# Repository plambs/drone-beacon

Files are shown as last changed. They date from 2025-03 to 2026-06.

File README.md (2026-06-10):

# Drone beacon

## Description

This repository contain the source code and schematic of the drone beacon that is mandatory for all flying models over 800gr in France.
The beacon use a ESP32 to send the model id over wifi and a gps module to know it position.

All model must be registered on [AlphaTango](https://alphatango.aviation-civile.gouv.fr/login.jsp)

This work is based on the work done by Arnaud Mazin and the source of it can be found [here](https://www.club-modelisme-saclay.fr/ameliorations-balise-signalement-electronique-modeles-reduits-volants/)

## Build, flash and monitor

### Install ESP-IDF tools

Follow the [get-started](https://docs.espressif.com/projects/esp-idf/en/stable/esp32/get-started/linux-macos-setup.html) of the ESP IDF tools documentation.

For linux users
```
sudo apt-get install git wget flex bison gperf python3 python3-pip python3-venv cmake ninja-build ccache libffi-dev libssl-dev dfu-util libusb-1.0-0

mkdir -p ~/esp
cd ~/esp
git clone -b v5.4.3 --recursive https://github.com/espressif/esp-idf.git

cd ~/esp/esp-idf
./install.sh esp32
```

After that when you want to use the ESP-IDF tools you only need to source the export.sh script.
```
. $HOME/esp/esp-idf/export.sh
```

### Init submodule

```
git submodule update --init --recursive
```

### Beacon

```
cd sources/beacon
idf.py build
idf.py flash
```

Balise status code
|Status|Fast blink|Slow blink|
|---|---|---|
|Reset GPS|4||
|No position|3||
|Position but no home (not enough precision)|2||
|Trasmiting beacon (beacon is working)||1|

Initialisation time take at least 2 minute in ideal condition

### Receiver

```
cd sources/receiver
idf.py build
idf.py flash
```

### Monitor the serial output

```
idf.py monitor
```
To exit the monitor use Ctrl+T Ctrl+X

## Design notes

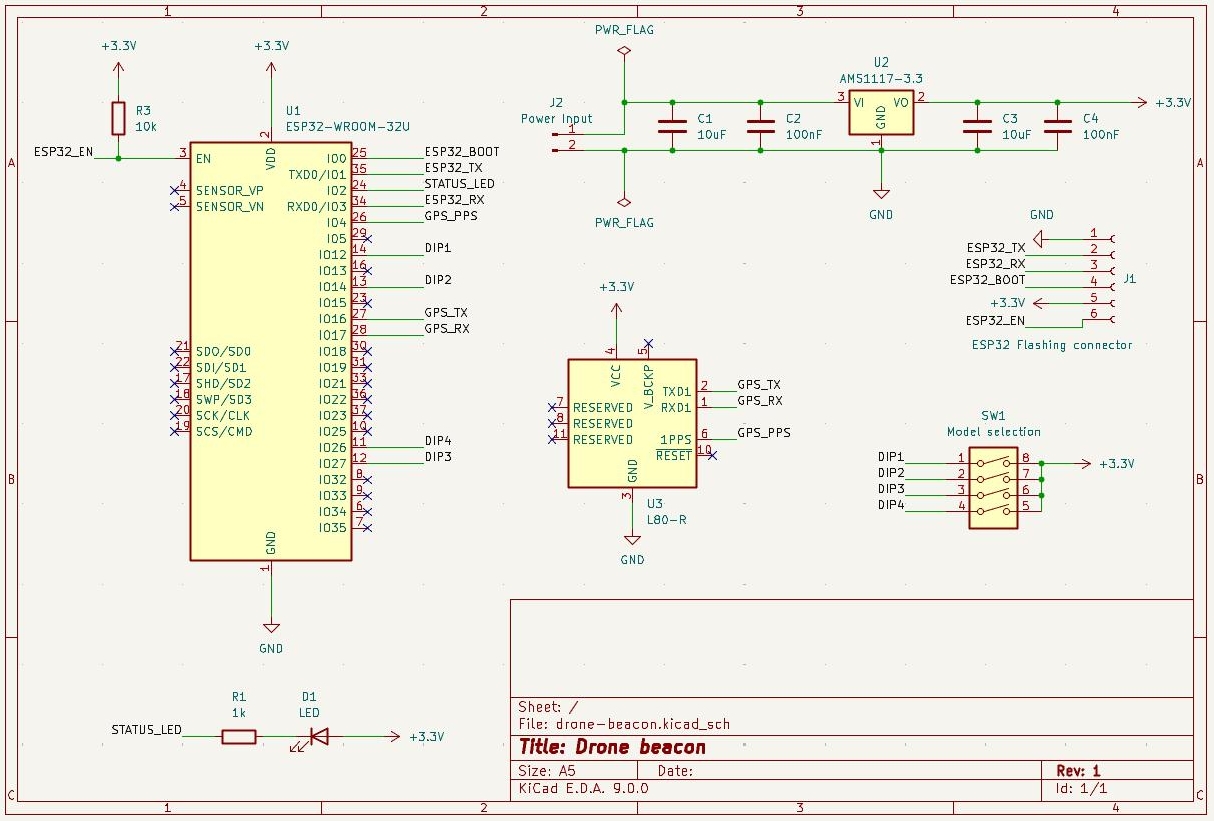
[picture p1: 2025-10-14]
documentation/images/schematic.jpeg

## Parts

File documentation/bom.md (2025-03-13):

# Bill of material

## Description

This is the list of all the components needed to build the beacon.

## List of hardware needed

| Designator | Hardware | Footprint (metric) | Quantity | Link | Notes |
|---|---|---|---|---|---|
| PCB | NA | NA | 1 | NA | Take the pcb manufactor you prefere |
| U1 | ESP32 WROOM 32U | NA | 1 | TODO | 4MB is enough |
| U3 | Quectel L96 | NA | 1 | TODO | / |
| U2 | AMS1117 | SOT223 | 1 | TODO | / |
| C1, C3 | Capacitor 10uF  | 0201 (0603) | 2 | TODO | / |
| C2, C4 | Capacitor 100nF | 0201 (0603) | 2 | TODO | / |
| D1 | Led | 0201 (0603) | 1 | TODO | / |
| R1 | Resistor 1k | 0201 (0603) | 1 | TODO | / |
| R3 | Resistor 10k | 0201 (0603) | 1 | TODO | / |
| J1 | JST 1x06 | JST 1x06 P1.00mm | 1 | TODO | / |
| J2 | PinHeader | 1x02 P2.00mm | 0 | TODO | Leave it empty |
| SW1 | Dip switch x04  | SMD pitch 1.27mm | 1 | TODO | / |

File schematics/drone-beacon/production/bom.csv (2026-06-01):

Designator | Footprint | Quantity | Value | LCSC Part #
C1, C3, C8 | 0402 | 3 | 10uF
C2, C4 | 0402 | 2 | 100nF
C5, C6, C7 | 0402 | 3 | 0.1uF
D1 | 0402 | 1 | LED
J1 | JST_SHL_SM06B-SHLS-TF_1x06-1MP_P1.00mm_Horizontal | 1 | ESP32 Flashing connector
J2 | PinHeader_1x02_P2.00mm_Vertical | 1 | Power Input
R1 | 0402 | 1 | 1k
R3 | 0402 | 1 | 10k
SW1 | SW_DIP_SPSTx04_Slide_Copal_CHS-04B_W7.62mm_P1.27mm | 1 | Model selection
TP1, TP2, TP3, TP4, TP5, TP6, TP7, TP8, TP9 | TestPoint_Pad_D1.0mm | 9 | TestPoint
U1 | ESP32-WROOM-32U | 1 | ESP32-WROOM-32U
U2 | SOT-223 | 1 | AMS1117-3.3
U3 | Quectel_L96 | 1 | L96

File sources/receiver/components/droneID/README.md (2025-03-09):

# droneID_FR

[https://github.com/khancyr/droneID_FR](https://github.com/khancyr/droneID_FR)

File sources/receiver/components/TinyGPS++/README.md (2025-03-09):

# TinyGPSPlus

[https://github.com/mikalhart/TinyGPSPlus](https://github.com/mikalhart/TinyGPSPlus)

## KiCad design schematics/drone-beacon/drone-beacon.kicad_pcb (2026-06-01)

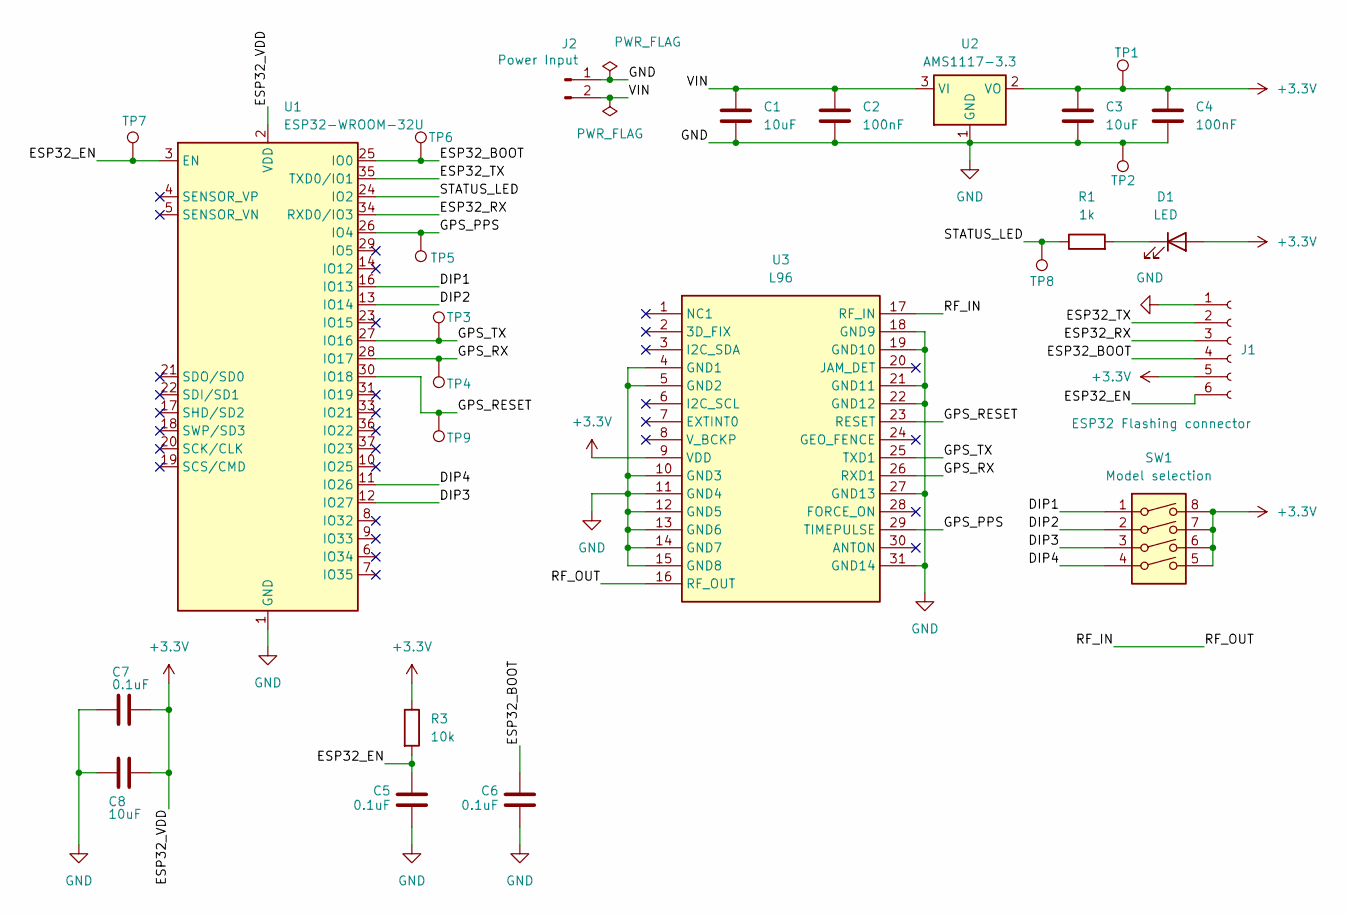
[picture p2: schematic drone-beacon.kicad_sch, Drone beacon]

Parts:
C1, C3, C8: 10uF; C_0402_1005Metric_Pad0.74x0.62mm_HandSolder
C2, C4: 100nF; C_0402_1005Metric_Pad0.74x0.62mm_HandSolder
C5, C6, C7: 0.1uF; C_0402_1005Metric_Pad0.74x0.62mm_HandSolder
D1: LED; LED_0402_1005Metric_Pad0.77x0.64mm_HandSolder
J1: ESP32 Flashing connector; JST_SHL_SM06B-SHLS-TF_1x06-1MP_P1.00mm_Horizontal
J2: Power Input; PinHeader_1x02_P2.00mm_Vertical
R1: 1k; R_0402_1005Metric_Pad0.72x0.64mm_HandSolder
R3: 10k; R_0402_1005Metric_Pad0.72x0.64mm_HandSolder
SW1: Model selection; SW_DIP_SPSTx04_Slide_Copal_CHS-04B_W7.62mm_P1.27mm
TP1, TP2, TP3, TP4, TP5, TP6, TP7, TP8, TP9: TestPoint; TestPoint_Pad_D1.0mm
U1: ESP32-WROOM-32U
U2: AMS1117-3.3; SOT-223
U3: L96; Quectel_L96; Mouser Part Number 277-L96-M33

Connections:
+3.3V: C3.1, C4.1, C7.1, C8.1, D1.2 (A), J1.5, R3.1, SW1.5, SW1.6, SW1.7, SW1.8, TP1.1, U1.2 (VDD), U2.2 (VO), U3.9 (VDD)
/DIP1: SW1.1, U1.16 (IO13)
/DIP2: SW1.2, U1.13 (IO14)
/DIP3: SW1.3, U1.12 (IO27)
/DIP4: SW1.4, U1.11 (IO26)
/ESP32_BOOT: C6.1, J1.4, TP6.1, U1.25 (IO0)
/ESP32_EN: C5.1, J1.6, R3.2, TP7.1, U1.3 (EN)
/ESP32_RX: J1.3, U1.34 (RXD0/IO3)
/ESP32_TX: J1.2, U1.35 (TXD0/IO1)
/GPS_PPS: TP5.1, U1.26 (IO4), U3.29 (TIMEPULSE)
/GPS_RESET: TP9.1, U1.30 (IO18), U3.23 (RESET)
/GPS_RX: TP4.1, U1.28 (IO17), U3.26 (RXD1)
/GPS_TX: TP3.1, U1.27 (IO16), U3.25 (TXD1)
/RF_IN: U3.16 (RF_OUT), U3.17 (RF_IN)
/STATUS_LED: R1.1, TP8.1, U1.24 (IO2)
/VIN: C1.1, C2.1, J2.2, U2.3 (VI)
GND: C1.2, C2.2, C3.2, C4.2, C5.2, C6.2, C7.2, C8.2, J1.1, J2.1, TP2.1, U1.1 (GND), U1.15 (GND), U1.38 (GND), U1.39 (GND), U2.1 (GND), U3.4 (GND1), U3.5 (GND2), U3.10 (GND3), U3.11 (GND4), U3.12 (GND5), U3.13 (GND6), U3.14 (GND7), U3.15 (GND8), U3.18 (GND9), U3.19 (GND10), U3.21 (GND11), U3.22 (GND12), U3.27 (GND13), U3.31 (GND14)
unnamed: D1.1 (K), R1.2

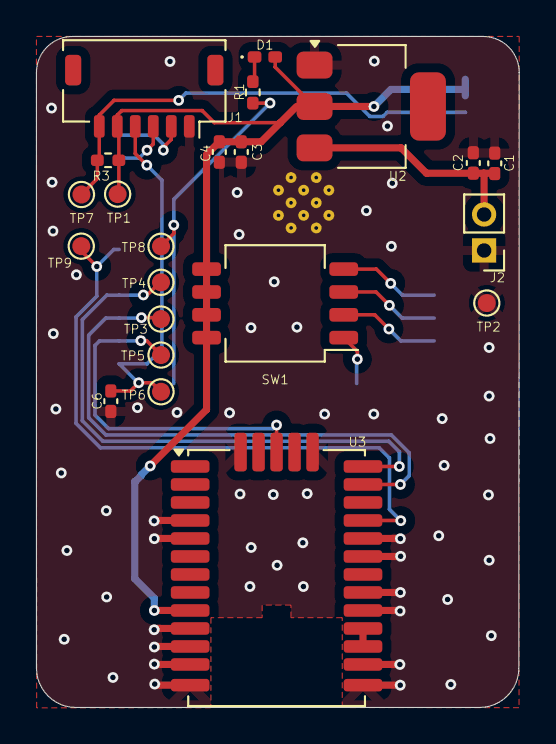
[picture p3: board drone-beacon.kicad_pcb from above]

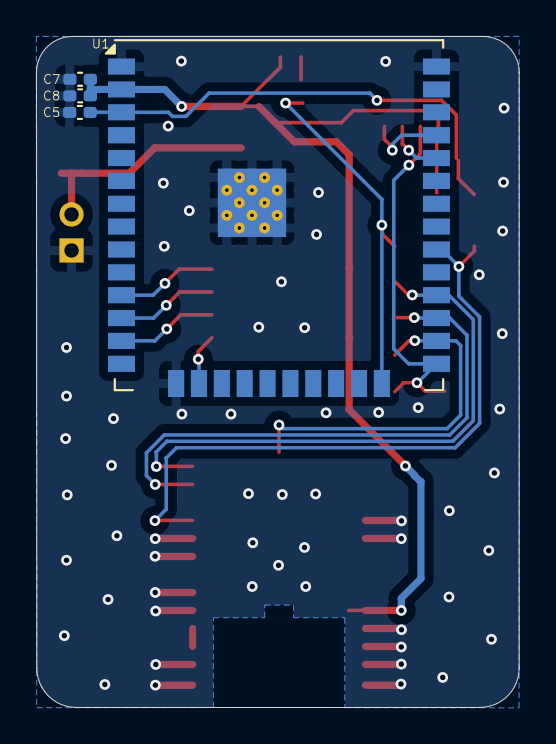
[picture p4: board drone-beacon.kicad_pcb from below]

Board: 2 copper layers, 26.8 x 37.3 mm, 26 parts (4 on the bottom side), 18 nets.

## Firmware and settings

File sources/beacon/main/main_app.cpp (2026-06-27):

/*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
 *  Used with ESP32 + BN220, modified by Julien Launay 14/09/2020
 *  Using https://github.com/khancyr/TTGO_T_BEAM/tree/master/src. Thanks to Pierre Khancyr the original author of this project.
 *  With https://github.com/f5soh/balise_esp32/blob/droneID_FR_testing/droneID_FR.h
 */

#include "nvs_flash.h"
#include "esp_wifi.h"
#include "esp_event.h"
#include "esp_netif.h"

#include "esp_sleep.h"
#include "esp_timer.h"

#include "driver/gpio.h"

#include "led.h"
#include "gps.h"
#include "beacon.h"
#include "config.h"
#include "nmea.h"

#include "log.h"

/* Forward declaration using the extern C so esp-idf can link */
extern "C" {
	void app_main(void);
}

static int _init_minimal_system()
{
	int ret = 0;

	// 1. Init NVS
	ret = nvs_flash_init();

	if (ret == ESP_ERR_NVS_NO_FREE_PAGES ||
			ret == ESP_ERR_NVS_NEW_VERSION_FOUND)
	{
		ret = nvs_flash_erase();
		fail_if_not_zero(ret, -1, "nvs_flash_erase failed, returned: %d\n", ret);
		ret = nvs_flash_init();
	}

	fail_if_not_zero(ret, -2, "nvs_flash_init failed, returned: %d\n", ret);

	// 2. Init TCP/IP stack
	ret = esp_netif_init();
	fail_if_not_zero(ret, -3, "esp_netif_init failed, returned: %d\n", ret);

	// 3. Init event loop
	ret = esp_event_loop_create_default();
	fail_if_not_zero(ret, -4, "esp_event_loop_create_default failed, returned: %d\n", ret);

	return 0;
}

#if SLEEP_MODE_ENABLED
#define WAKEUP_GPIO GPIO_NUM_4
static int _setup_sleep()
{
	int ret = 0;

	// Configure the chip to wakeup when the wakeup pin in pulled high (PPS froom GPS module).
    gpio_config_t io_conf = {};
    io_conf.intr_type = GPIO_INTR_DISABLE;
    io_conf.mode = GPIO_MODE_INPUT;
    io_conf.pin_bit_mask = (1ULL << WAKEUP_GPIO);
    io_conf.pull_down_en = GPIO_PULLDOWN_ENABLE;
    io_conf.pull_up_en = GPIO_PULLUP_DISABLE;

    ret = gpio_config(&io_conf);
    fail_if_not_zero(ret, -1, "gpio_config failed, returned: %d\n", ret);

	// Wake when GPIO4 goes HIGH
    ret = esp_sleep_enable_ext0_wakeup(WAKEUP_GPIO, 1);
    fail_if_not_zero(ret, -2, "esp_sleep_enable_ext0_wakeup failed, returned: %d\n", ret);

	// Also configure the chip to wakeup when the uart received some data.
	// TODO check if uart2 can wake up the chip

	return 0;
}
#endif

#if SLEEP_MODE_ENABLED
static int _flush_logs(void)
{
	int ret = 0;
	ret = fflush(stdout);
	fail_if_not_zero(ret, -1, "fflush failed, returned: %d\n", ret);
	return 0;
}
#endif

#if SLEEP_MODE_ENABLED
static int _go_to_sleep()
{
	int ret = 0;

	// Prevent immediate wakeup
	while (gpio_get_level(WAKEUP_GPIO))
	{
		vTaskDelay(pdMS_TO_TICKS(1));
	}

	// Stop wifi
	ret = esp_wifi_stop();
	fail_if_not_zero(ret, -1, "esp_wifi_stop failed, returned: %d\n", ret);

#if DEBUG_DISPLAY_SLEEP_LOGS
	log_debug("Entering light sleep...\n");
#endif

	ret = _flush_logs();
	fail_if_negative(ret, -2, "_flush_logs failed, returned: %d\n", ret);

#if DEBUG_DISPLAY_WAKE_UP_SOURCE_AND_DURATION
	int64_t t0 = esp_timer_get_time();
#endif

	// Go to sleep, this function will return when we wakeup.
	ret = esp_light_sleep_start();
	fail_if_not_zero(ret, -3, "esp_light_sleep_start failed, returned: %d\n", ret);

#if DEBUG_DISPLAY_WAKE_UP_SOURCE_AND_DURATION
	int64_t t1 = esp_timer_get_time();
#endif

#if DEBUG_DISPLAY_SLEEP_LOGS
	log_debug("Wakeup!\n");
#endif

#if DEBUG_DISPLAY_WAKE_UP_SOURCE_AND_DURATION
	log_debug("Sleep duration: %.3f ms\n", (t1 - t0) / 1000.0);

	esp_sleep_wakeup_cause_t cause = esp_sleep_get_wakeup_cause();
	if (cause == ESP_SLEEP_WAKEUP_EXT0)
	{
		log_debug("Wakeup from GPIO4 pulse\n");
	}
	else
	{
		log_debug("Other wake up source: %d\n", cause);
	}
#endif

	// Restart wifi
	ret = esp_wifi_start();
	fail_if_not_zero(ret, -4, "esp_wifi_start failed, returned: %d\n", ret);

	return 0;
}
#endif

void app_main(void)
{
	int ret = 0;

	ret = _init_minimal_system();
	log_if_negative(ret, "_init_minimal_system failed, returned: %d\n", ret);

#if SLEEP_MODE_ENABLED
	ret = _setup_sleep();
	log_if_negative(ret, "_setup_sleep failed, returned: %d\n", ret);
#endif

	log("Start main application\n");

	ret = led_init();
	log_if_negative(ret, "led_init failed, returned: %d\n", ret);

	ret = gps_init();
	log_if_negative(ret, "gps_init failed, returned: %d\n", ret);

	ret = beacon_init();
	log_if_negative(ret, "beacon_init failed, returned: %d\n", ret);

	log_info("Init phase done, go in mainloop\n");

	while(1)
	{
		/**
		 * Run the gps mainloop, this get the char sended by the gps module,
		 * decode them and get all the usefull information for the beacon.
		 */
		ret = gps_get_data();
		log_if_negative(ret, "gps_get_data failed, returned: %d\n", ret);

		// if gps is dead -> todo reset and reconfigure gps
		if(gps_need_reset())
		{
			// Print info log
			log_error("No GPS detected\n");

			// Turn off the led when the beacon is not working.
			ret = led_blink(4);
			log_if_negative(ret, "led_blink failed, returned: %d\n", ret);

			// Reset of the gps module
			ret = gps_reset();
			log_if_negative(ret, "gps_reset failed, returned: %d\n", ret);

			// Wait some time then retry to get gps data
			vTaskDelay(pdMS_TO_TICKS(DELAY_BEFORE_RELOOPING_MS));
			continue;
		}

		// print number satelite, fix, home status and if data must be send
		log_info("sat view: %d, sat fix: %d, hdop: %0.2f, home set: %d\n",
			nmea_get_satellites_in_view(),
			gps_get_satellites(),
			gps_get_precision(),
			beacon_is_home_set()
		);

		// if no position -> new try later
		if(!gps_position_detected())
		{
			// Blink the led
			ret = led_blink(3);
			log_if_negative(ret, "led_blink failed, returned: %d\n", ret);

			log_warn("Position unknown\n");

			// Position is not detected yet, we enable sleep mode only if position
			// is knowed, this assure us the gps module is working correctly. The no
			// position state should not exceed 3 min in correct condition so the power
			// usage is limited
			// Wait some time then retry to get gps data
			vTaskDelay(pdMS_TO_TICKS(DELAY_BEFORE_RELOOPING_NO_SLEEP_MS));
			continue;
		}

		// if position and no home -> set home
		if(!beacon_is_home_set())
		{
			// Blink the led
			ret = led_blink(2);
			log_if_negative(ret, "led_blink failed, returned: %d\n", ret);

			log_info("Position detected but no home set\n");

			// job done, go to sleep;
			goto main_sleep;
		}

		// if home and it time to send beacon -> send beacon data
		if(beacon_data_must_be_send())
		{
			// toggle the LED to see beacon sended
			ret = led_toggle_state();
			log_if_negative(ret, "led_toggle_state failed, returned: %d\n", ret);

			log_info("Send beacon\n");

			// Send the drone identification frame
			ret = beacon_send_data();
			log_if_negative(ret, "beacon_send_data failed, returned: %d\n", ret);
		}

main_sleep:
		/** Wait 10ms before going to the next iteration of the loop so the system can do something else
		 * like kicking the watchdog
		 */
		vTaskDelay(pdMS_TO_TICKS(DELAY_BEFORE_RELOOPING_MS));

#if SLEEP_MODE_ENABLED
		ret = _go_to_sleep();
		log_if_negative(ret, "_go_to_sleep failed, returned: %d\n", ret);
#else
		vTaskDelay(pdMS_TO_TICKS(DELAY_BEFORE_RELOOPING_NO_SLEEP_MS));
#endif
	}
}

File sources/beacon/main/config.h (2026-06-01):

#ifndef _CONFIG_HEADER_
#define _CONFIG_HEADER_

#define SERIAL_DEFAUT_BAUDRATE 115200

/*
 * Name of the acces point
 */
#define BEACON_SSID "DroneBeacon"

/*
 * Access point password
 */
#define BEACON_PASSWORD "123456789"

/*
 * Beacon ID, change it by the one received on Alphatango.
 *
 * ID format is like that: 000 AM1 00000000 G MMM XXXXXXXXXXXX
 * 000 is the beacon builder id, for homemade one we must use 000
 * AM1 is the beacon model id (put whatever you want)
 * 00000000 don't change it.
 * XXXXXXXXXXXX will be replaced with the BEACON_ID set in config.h or the MAC address of the ESP32.
 * G will be replaced with the model group
 * MMM will be replaced by the model mass
 * - 002 (group 0)
 * - 004 (group 1)
 * - 025 (group 2)
 * - 150 (group 3)
 */
#define BEACON_BUILDER_ID "000" // Homemade always use 000
#define BEACON_MODEL_ID "DB1" // Put whatever you want, lengh max 3 chars
#define BEACON_ID "" // If empty the system use the MAC addess, if you put a custom one, lengh max 11 chars
#define BEACON_ID_FULL_LENGTH 31

#define WANTED_SATELLITES 5 // Value must be equal or higher to be valid
#define WANTED_PRECISION 3.0 // Value must be lower than that to be valid
#define LOG_PERIOD_MS 1000 // print log every second
#define DELAY_BEFORE_RELOOPING_MS 10 // ms
#define SLEEP_MODE_ENABLED 1
#define DELAY_BEFORE_RELOOPING_NO_SLEEP_MS 500 //ms

// Hardware debug define
#define DEBUG_DISPLAY_SATELLITE_AND_SNR_DETAILS 0
#define DEBUG_DISPLAY_RAW_NMEA_RECEIVED_FROM_GPS 0
#define DEBUG_DISPLAY_GPS_DATA 0
#define DEBUG_DISPLAY_HOME_STATUS 0
#define DEBUG_DISPLAY_BEACON_PACKET 0
#define DEBUG_DISPLAY_BEACON_DATA 1
#define DEBUG_DISPLAY_DETAILS_SAT_SNR 0
#define DEBUG_DISPLAY_WAKE_UP_SOURCE_AND_DURATION 0
#define DEBUG_DISPLAY_SLEEP_LOGS 0

#endif //_CONFIG_HEADER_

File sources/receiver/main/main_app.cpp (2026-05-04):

/* Decode beacon trame balise
 *  Set outil/partition schem/No OTA 2MB APP/2MB SPIFFS
 *  Receive data from wifi beacon from emetter
 *  Send data over BLE to Android application
 *  Version 1/11/2020
 */

#include <Arduino.h>
#include <esp_wifi.h>
#include <esp_event.h>
#include <nvs_flash.h>
#include <esp_netif.h>
#include "lvgl.h"

String trame;

/**
  * Enumeration des types de données à envoyer
*/
enum DATA_TYPE: uint8_t {
  RESERVED = 0,
  PROTOCOL_VERSION = 1,
  ID_FR = 2,
  ID_ANSI_CTA = 3,
  LATITUDE = 4,        // In WS84 in degree * 1e5
  LONGITUDE = 5,       // In WS84 in degree * 1e5
  ALTITUDE = 6,        // In MSL in m
  HEIGTH = 7,          // From Home in m
  HOME_LATITUDE = 8,   // In WS84 in degree * 1e5
  HOME_LONGITUDE = 9,  // In WS84 in degree * 1e5
  GROUND_SPEED = 10,   // In m/s
  HEADING = 11,        // Heading in degree from north 0 to 359.
  NOT_DEFINED_END = 12,
};

/**
  * Tableau TLV (TYPE, LENGTH, VALUE) avec les tailles attendu des différents type données.
***/
static constexpr uint8_t TLV_LENGTH[] {
  0,  // [DATA_TYPE::RESERVED]
  1,  // [DATA_TYPE::PROTOCOL_VERSION]
  30, // [DATA_TYPE::ID_FR]
  0,  // [DATA_TYPE::ID_ANSI_CTA]
  4,  // [DATA_TYPE::LATITUDE]
  4,  // [DATA_TYPE::LONGITUDE]
  2,  // [DATA_TYPE::ALTITUDE]
  2,  // [DATA_TYPE::HEIGTH]
  4,  // [DATA_TYPE::HOME_LATITUDE]
  4,  // [DATA_TYPE::HOME_LONGITUDE]
  1,  // [DATA_TYPE::GROUND_SPEED]
  2,  // [DATA_TYPE::HEADING]
};


typedef struct {
  unsigned frame_ctrl:16;
  unsigned duration_id:16;
  uint8_t addr1[6]; /* receiver address */
  uint8_t addr2[6]; /* sender address */
  uint8_t addr3[6]; /* filtering address */
  unsigned sequence_ctrl:16;
  uint8_t addr4[6]; /* optional */
} wifi_ieee80211_mac_hdr_t;


typedef struct  {
  int16_t fctl;
  int16_t duration;
  uint8_t da;
  uint8_t sa;
  uint8_t bssid;
  int16_t seqctl;
  unsigned char *payload;
} __attribute__((packed)) WifiMgmtHdr;

typedef struct {
  WifiMgmtHdr hdr;
  uint8_t *payload;
} wifi_ieee80211_packet_t;

static void wifi_sniffer_init(void);
static void wifi_sniffer_set_channel(uint8_t channel);
static const char *wifi_sniffer_packet_type2str(wifi_promiscuous_pkt_type_t type);
static void wifi_sniffer_packet_handler(void *buff, wifi_promiscuous_pkt_type_t type);
void beaconCallback(void* buf, wifi_promiscuous_pkt_type_t type);

void wifi_sniffer_init(void)
{
  nvs_flash_init();
  esp_netif_init();
  ESP_ERROR_CHECK(esp_event_loop_create_default());
  wifi_init_config_t cfg = WIFI_INIT_CONFIG_DEFAULT();
  ESP_ERROR_CHECK(esp_wifi_init(&cfg) );
  ESP_ERROR_CHECK(esp_wifi_set_storage(WIFI_STORAGE_RAM) );
  ESP_ERROR_CHECK(esp_wifi_set_mode(WIFI_MODE_NULL) );
  ESP_ERROR_CHECK(esp_wifi_start() );
  esp_wifi_set_promiscuous(true);
  esp_wifi_set_promiscuous_rx_cb(&beaconCallback);
  
}

void wifi_sniffer_set_channel(uint8_t channel)
{
  esp_wifi_set_channel(channel, WIFI_SECOND_CHAN_NONE);
}

// Function to extract MAC addr from a packet at given offset
void getMAC(char *addr, uint8_t* data, uint16_t offset) {
  sprintf(addr, "%02x:%02x:%02x:%02x:%02x:%02x", data[offset+0], data[offset+1], data[offset+2], data[offset+3], data[offset+4], data[offset+5]);
}

static void printDataSpan(uint16_t start, int len, uint16_t size, uint8_t* data) {
  for(uint16_t i = start; i < len && i < start+size; i++) {
    Serial.write(data[i]);
    trame = trame + char(data[i]);
  }
}

static void printCoordinates(uint16_t start, int len, uint16_t size, uint8_t* data) {
  uint8_t count = size-1;
  int data_value = 0;
  //Serial.print(" data_value="); Serial.print(data_value); Serial.print(" neg=");
  bool neg_number = data[start] > 0x7F;
  //Serial.print(neg_number);Serial.print(" ");
  
  for(uint16_t i = start; i < len && i < start+size; i++) {
    //Serial.print(count); Serial.print("-");  
    data_value +=  (data[i]) << (8 * count); 
    count--;
  }
  
  if(neg_number) {
    data_value = (0xFFFFFFFF & ~data_value) + 1; 
    data_value *= -1;
  }
  
  Serial.print(double(data_value) * 0.00001 , 5);
  trame += String(double(data_value) * 0.00001,5);
}

static void printAltitude(uint16_t start, int len, uint16_t size, uint8_t* data) {
  uint8_t count = size-1;
  int data_value = 0;
  bool neg_number = data[start] > 0x7F;
  //Serial.print(neg_number);Serial.print(" ");
  
  for(uint16_t i = start; i < len && i < start+size; i++) {
    //Serial.print(count); Serial.print("-");  
    data_value +=  (data[i]) << (8 * count); 
    count--;
  }
  
  if(neg_number) {
    data_value = (0xFFFF & ~data_value) + 1; 
    data_value *= -1;
  }
  
  Serial.print(data_value);
  trame = trame + String(data_value);
}
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

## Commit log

2025-03-09 Rework receiver folder shape (WIP)
    [droneID_FR.h, main_app.cpp]
2025-03-12 Add kicad schematics for the drone-beacon
    [drone-beacon.kicad_pcb, drone-beacon.kicad_sch]
2025-03-13 Update schematics
    [drone-beacon.kicad_pcb, drone-beacon.kicad_sch]
2025-03-13 Publish pcb production files
    [bom.csv, designators.csv, positions.csv]
2025-03-13 Add BOM in documentation
2025-04-06 Update schematics (WIP)
    [drone-beacon.kicad_pcb, drone-beacon.kicad_sch]
2025-10-14 Update schematics v1
    [bom.csv, designators.csv, drone-beacon.kicad_pcb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]
2026-04-12 Fix some gps configuration issues
    [main_app.cpp]
2026-04-12 Cleanup and replace Serial.print* by printf
    [main_app.cpp]
2026-04-12 Print all sentence received and manually parse *GSV one
2026-05-03 Use define to enable/disable debug logs, cleanup some printf
2026-05-04 fix receiver build using esp-idf v5.4
    [main_app.cpp]
2026-05-16 move led management in its own source file
2026-06-01 schematics: update schematics and add missing pull up/down
    [bom.csv, designators.csv, drone-beacon.kicad_pcb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]
2026-06-11 beacon: replace most of arduino code by esp-idf one
    [beacon.cpp, gps.cpp, led.cpp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]
2026-06-27 beacon: replace printf by log_*
    [beacon.cpp, gps.cpp, main_app.cpp]
2026-06-27 beacon: change gps timming and flush uart at init

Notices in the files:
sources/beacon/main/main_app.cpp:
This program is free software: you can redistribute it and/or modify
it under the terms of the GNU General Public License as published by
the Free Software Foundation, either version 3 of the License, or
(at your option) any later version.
